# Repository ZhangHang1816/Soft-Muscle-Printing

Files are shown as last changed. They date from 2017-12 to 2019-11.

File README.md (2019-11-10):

# Soft-Muscle-Printing

This repository contains the code/data/model for printing Soft Artificial Muscle using Soft Muscle Printer.
The runnable jupyter notebook are [dog_bone muscle.ipynb](https://github.com/boxiXia/Soft-Muscle-Printing/blob/master/dog_bone%20muscle.ipynb) and [Soft_muscle_twisted spiral.ipynb](https://github.com/boxiXia/Soft-Muscle-Printing/blob/master/dog_bone%20muscle.ipynb)

### Graphical abstract
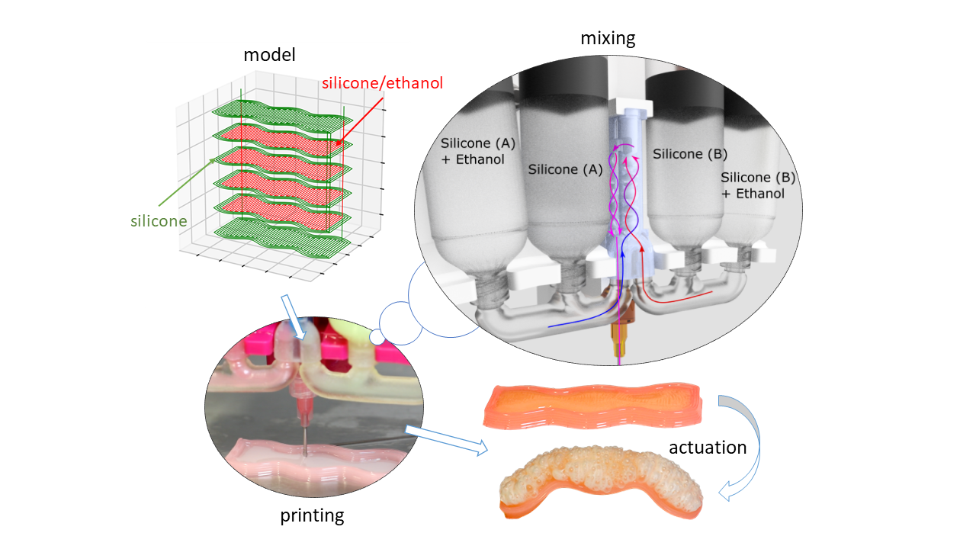
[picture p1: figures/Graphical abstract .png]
graphical abstract


### Photo of the soft muscle printer
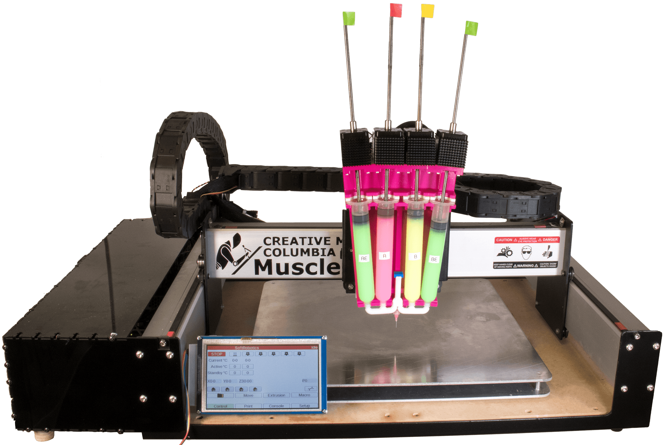
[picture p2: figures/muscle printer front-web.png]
Artificial muscle printer


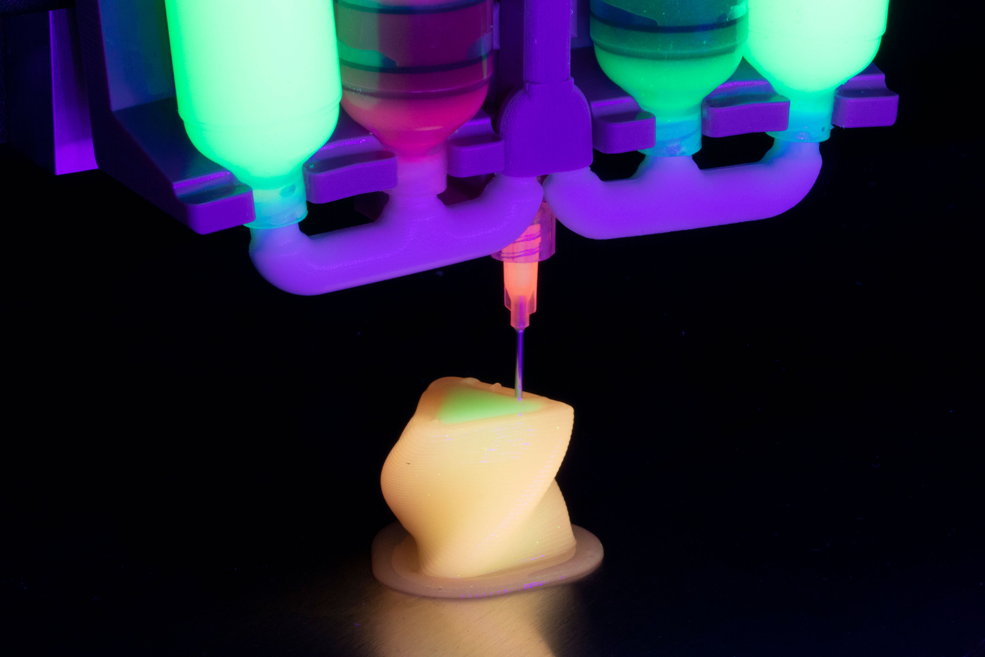
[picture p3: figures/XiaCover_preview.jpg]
printing rotating triangle


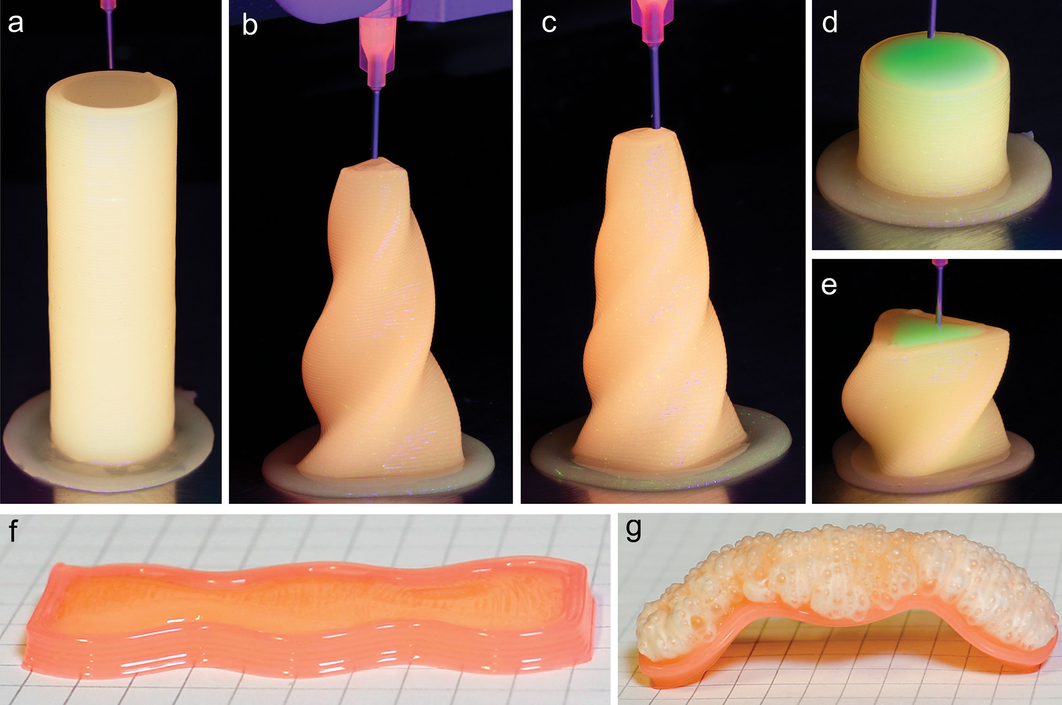
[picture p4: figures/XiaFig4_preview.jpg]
printed sturctures


### video of printing a muscle and actuating
supplementary - printing muscle and actuating (https://www.youtube.com/watch?v=KcunfdATq7U)

### video of printing complex structures
Supplementary - 3D Printing of Complex Shaped Structures (https://www.youtube.com/watch?v=6kZ5QKU3RHI)

### CAD and STL model of the mixer and electronics housing.
 
The raw Inventor model can be found in the [modeling](https://github.com/boxiXia/Soft-Muscle-Printing/tree/master/modeling) folder, which contains contains the 3d-printable and lasercut models to replicate the printer.

The mixer CAD model can be found in in [./modeling/mixer_design](https://github.com/boxiXia/Soft-Muscle-Printing/tree/master/modeling/mixer_design). The converted stl model can be found in [./modeling/mixer_design/stl_model](https://github.com/boxiXia/Soft-Muscle-Printing/tree/master/modeling/mixer_design/stl_model).
The CAD model for laser-cutting the electronics housing can be found in [modeling/lasercut_electronics_housing](https://github.com/boxiXia/Soft-Muscle-Printing/tree/master/modeling/lasercut_electronics_housing).
To open the CAD model (\*.ipt and \*.iam file), use [Autodesk Inventor 2019](https://www.autodesk.com/education/free-software/inventor-professional). The CAD models can also be found in [Grabcad](https://grabcad.com/library/soft-muscle-printer-1). 

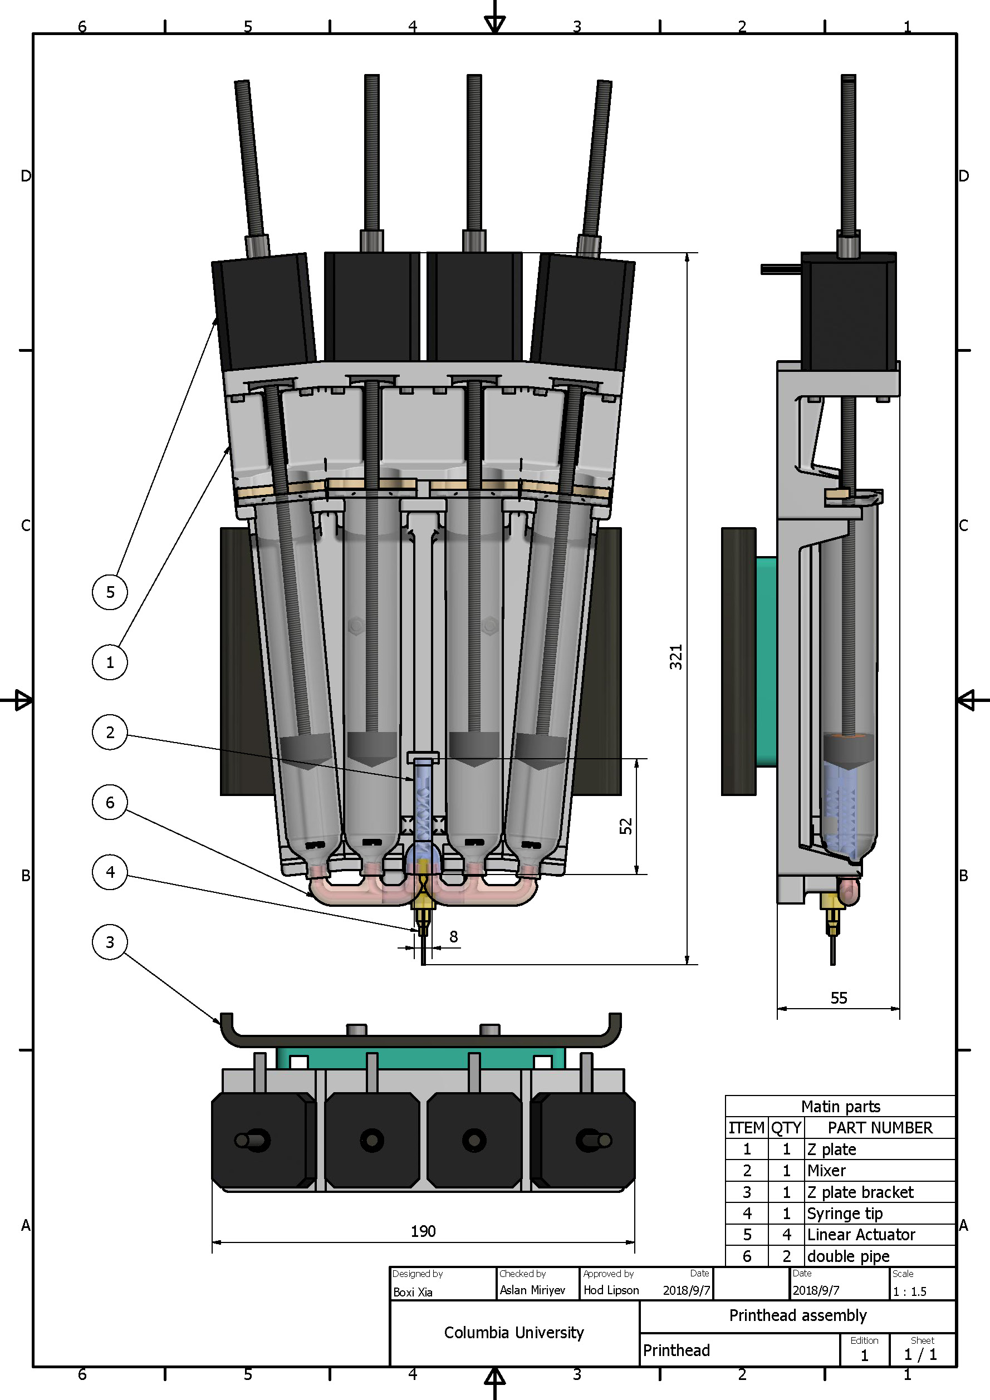
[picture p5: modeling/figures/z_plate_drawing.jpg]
assembly drwaing


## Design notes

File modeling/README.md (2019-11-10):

CAD model for the silicone muscle printer project @CreativeMachinesLab.

The folder "mixer_design" contains the Autodesk Inventor (2018) files for the mixing and printing module, the folder "stl_model" contains the exported ".stl" files of the printing module. The z plate assembly is printed with a Stratasys J750 printer in the Creative Machines Lab. The tubing is printed using "FLX9795-dm; Shore-A:95", the other parts are printed with "VeroPureWht." @boxiXia
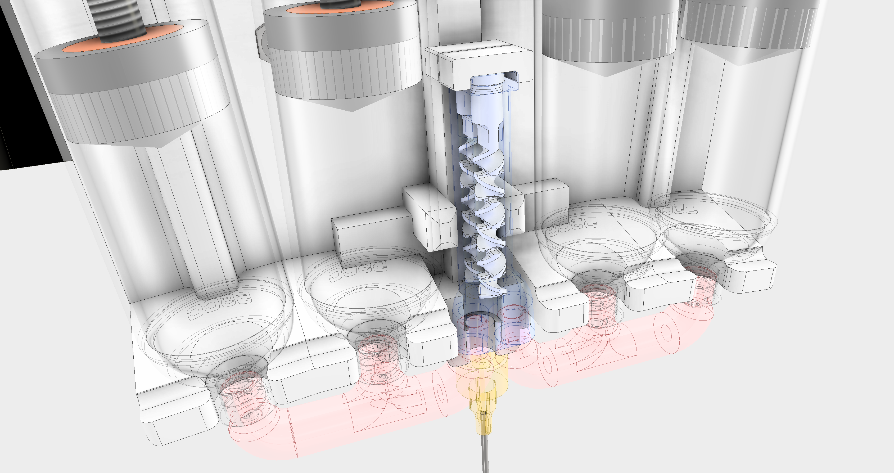
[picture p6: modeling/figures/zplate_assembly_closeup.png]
close up view of the z plate assembly


The folder "lasercut_electronics_housing" contains the electronic side mounting box model for the Shapeoko gantry. CAD files turned into two-dimensional drawing files are laser cut out of a 1/8 in a thick acrylic sheet. Two sheets about two feet long by 3 feet wide will be enough material for the entire assembly. The slots that connect the different sheets require 6-32 thread, ½ in long screws and 6-32 thread square nuts. Around 50 will be enough to assemble the housing. There are two square cutouts for installing fans used for cooling the control boards @jacobjoseph
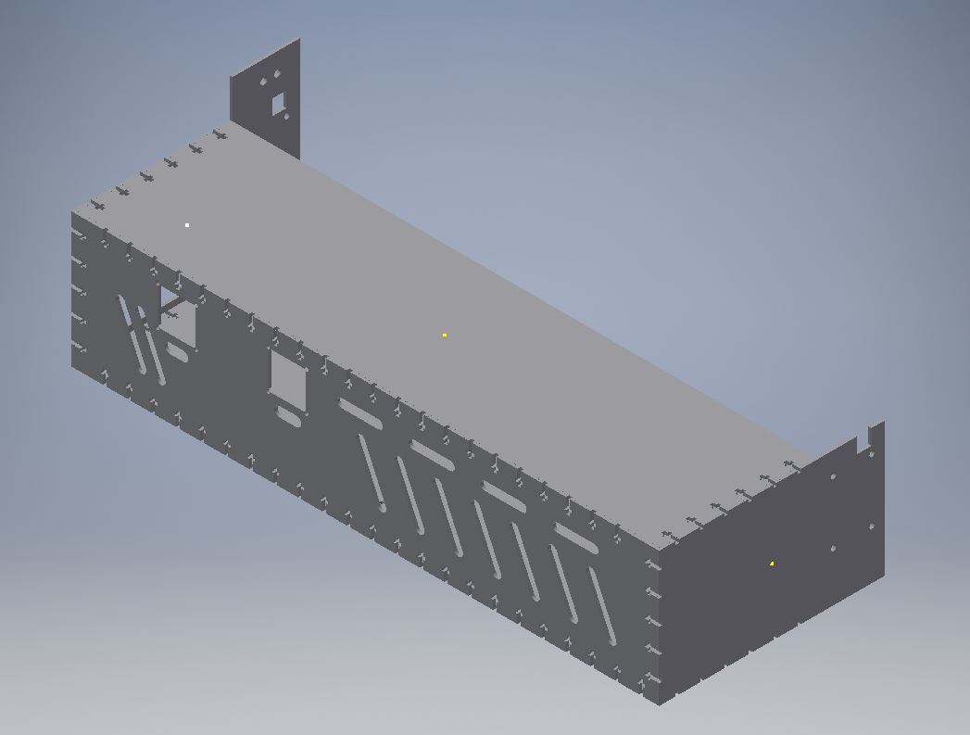
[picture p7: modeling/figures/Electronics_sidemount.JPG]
electronic side mount


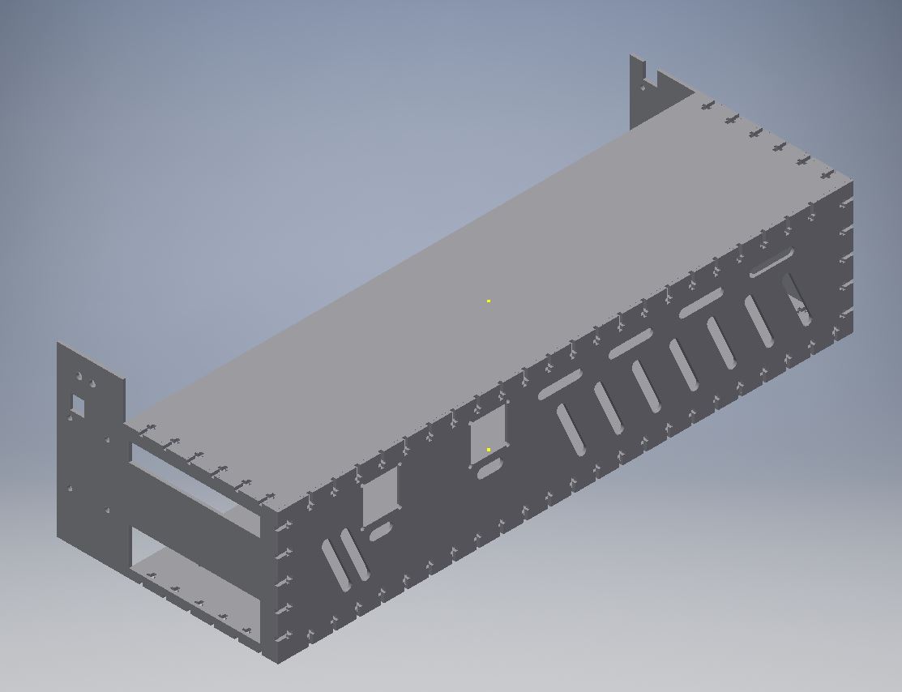
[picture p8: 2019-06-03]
modeling/figures/Electronics_sidemount_back.JPG

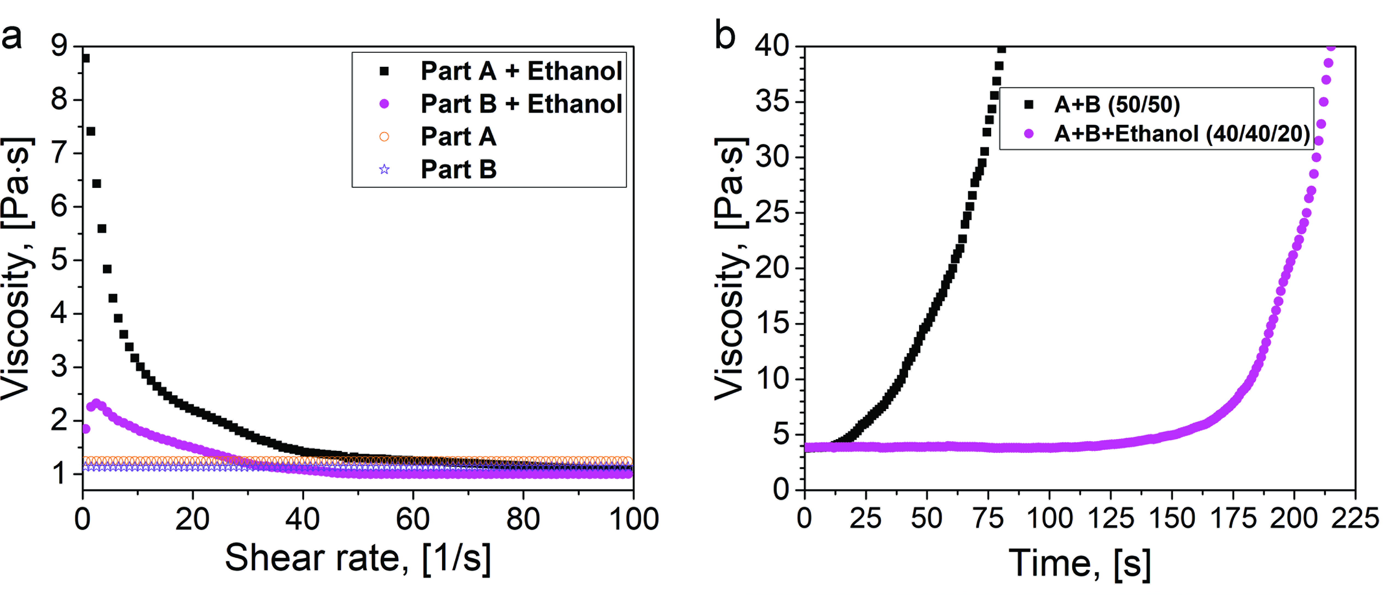
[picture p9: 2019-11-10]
figures/XiaFig5.tif

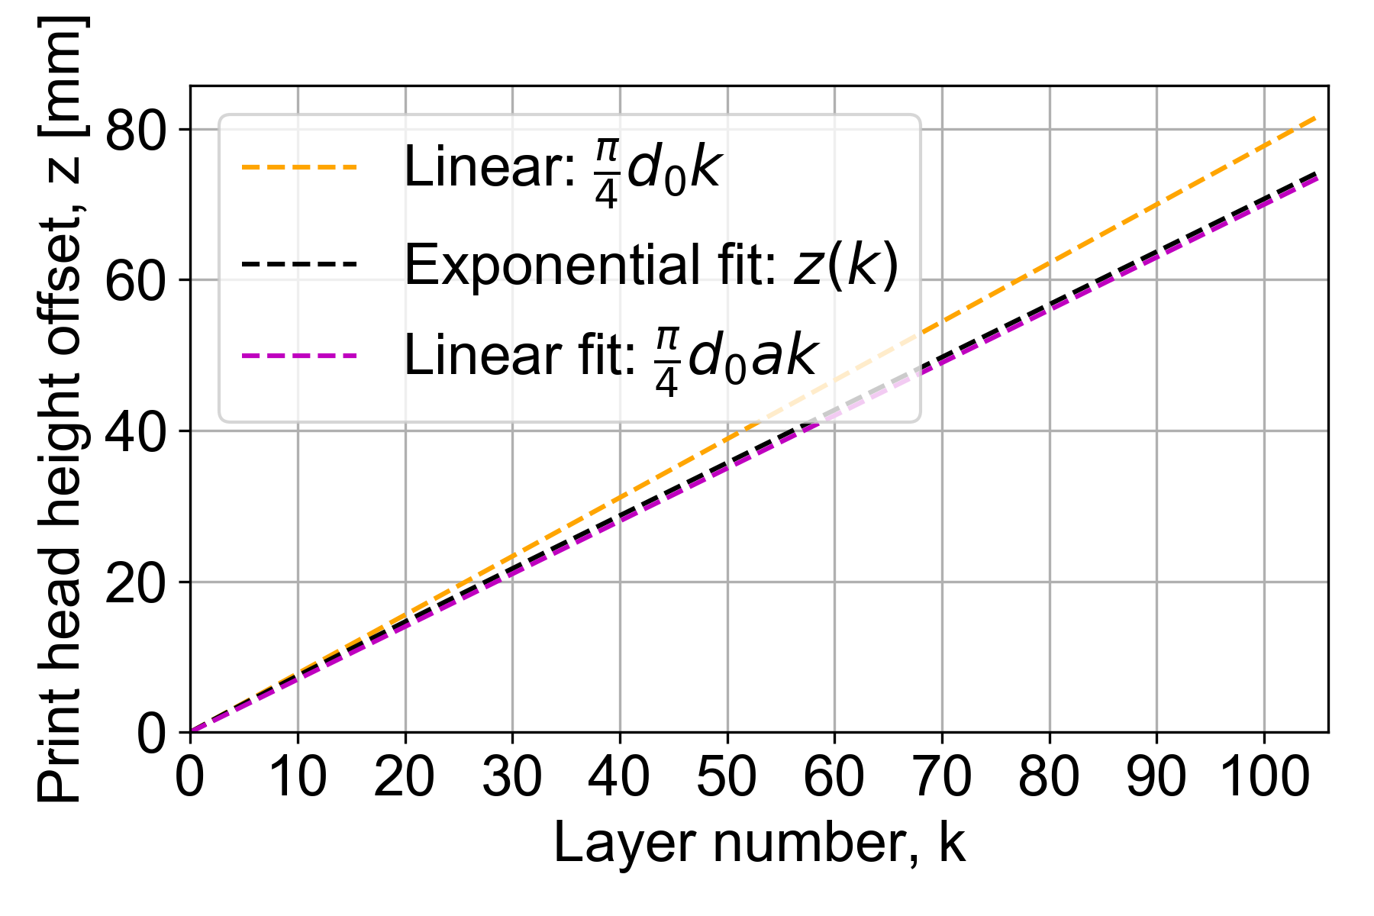
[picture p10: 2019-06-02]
figures/Z height Adjustment_a0.9_b0.1.png

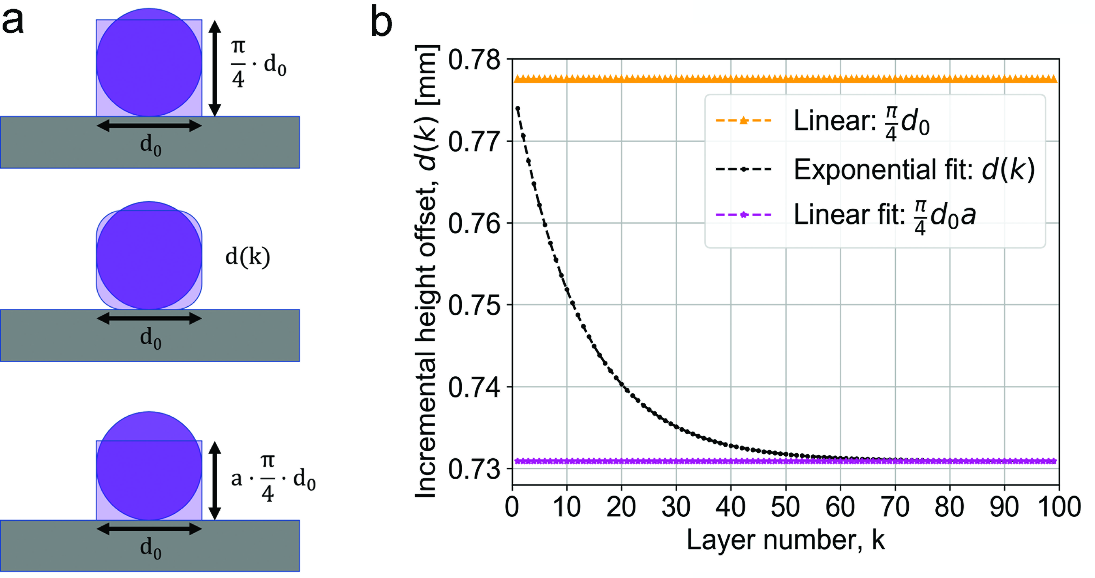
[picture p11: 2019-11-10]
figures/XiaFig3.tif

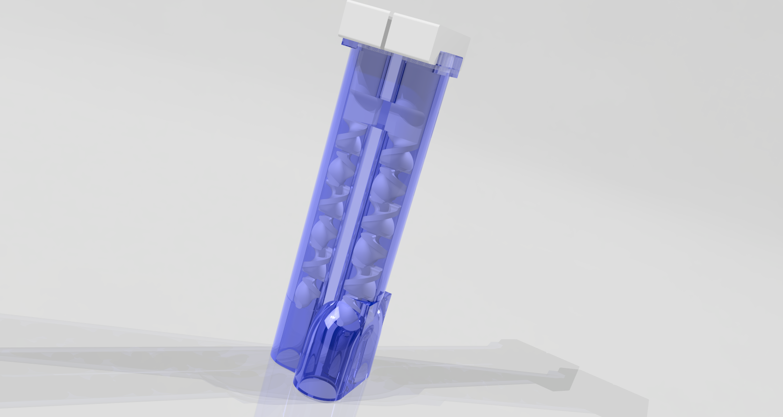
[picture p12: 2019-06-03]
modeling/figures/mixer.png

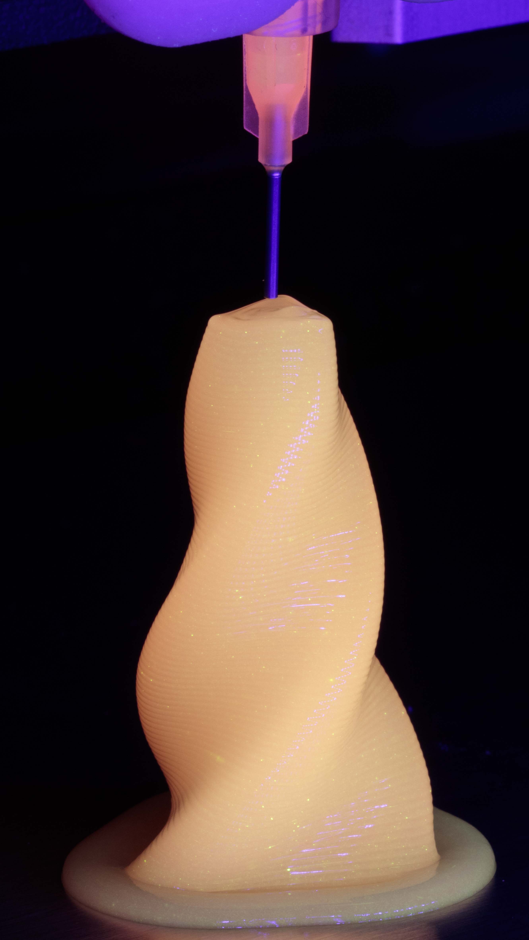
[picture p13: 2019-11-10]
figures/rotating triangle.jpg

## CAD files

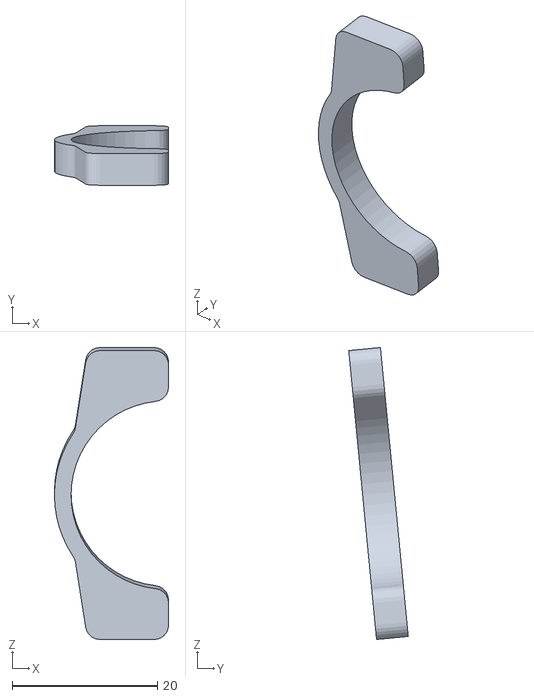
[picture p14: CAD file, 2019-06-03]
modeling/mixer_design/stl_model/zplate_assembly_syringe_stopper_x4.stl
15.7 x 8.21 x 40.2

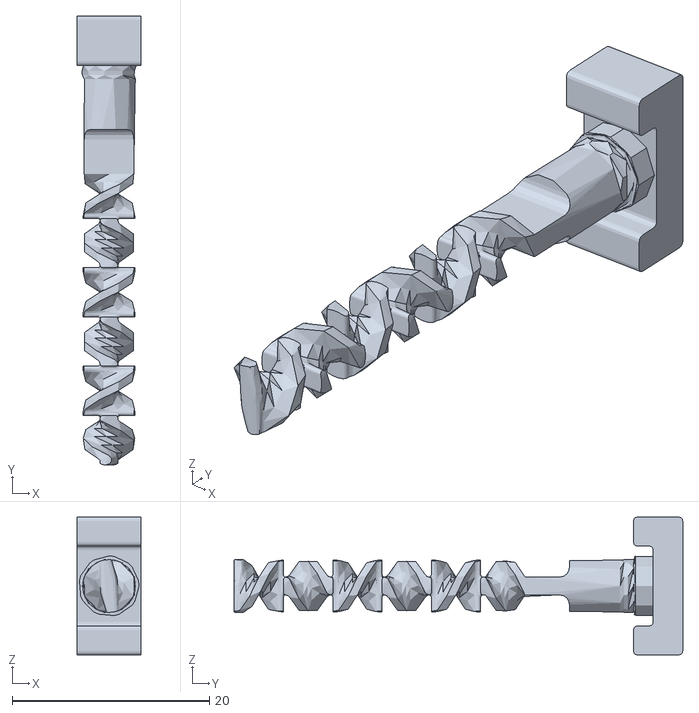
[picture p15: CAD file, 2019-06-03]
modeling/mixer_design/stl_model/zplate_assembly_mixer_core_x2.stl
6.50 x 45.5 x 14.0

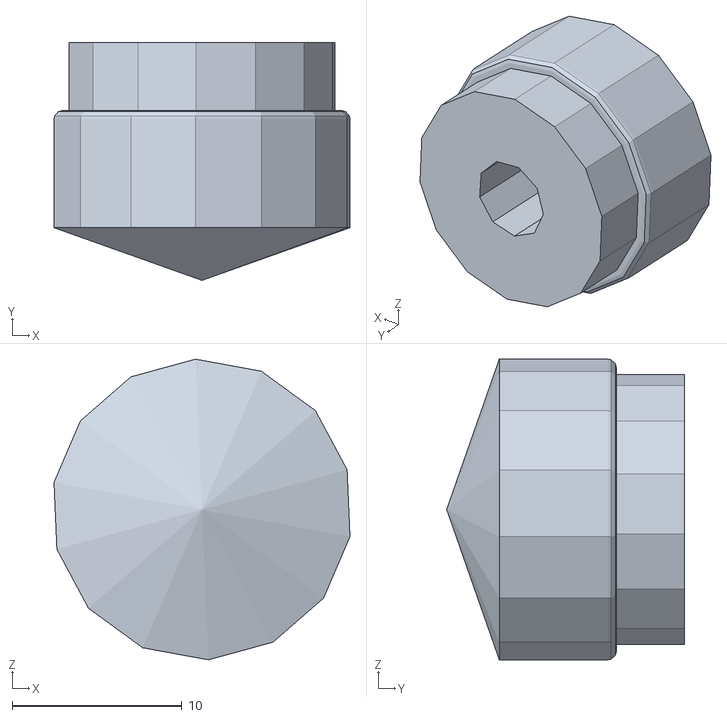
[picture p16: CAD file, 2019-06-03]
modeling/mixer_design/stl_model/zplate_assembly_plunger_adaptor_x4.stl
17.4 x 14.0 x 17.7

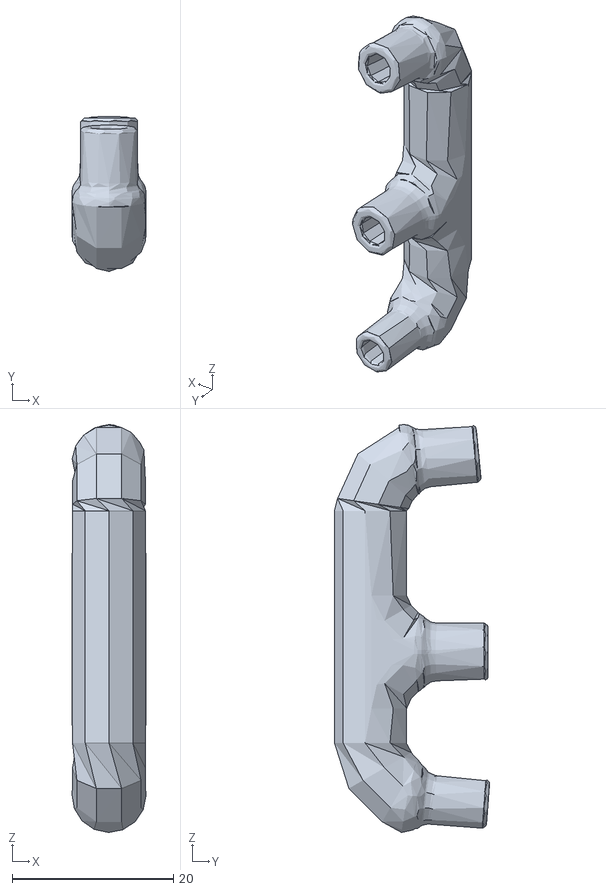
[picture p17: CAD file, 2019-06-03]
modeling/mixer_design/stl_model/zplate_assembly_doublePipe_v7.stl
9.20 x 19.3 x 50.7

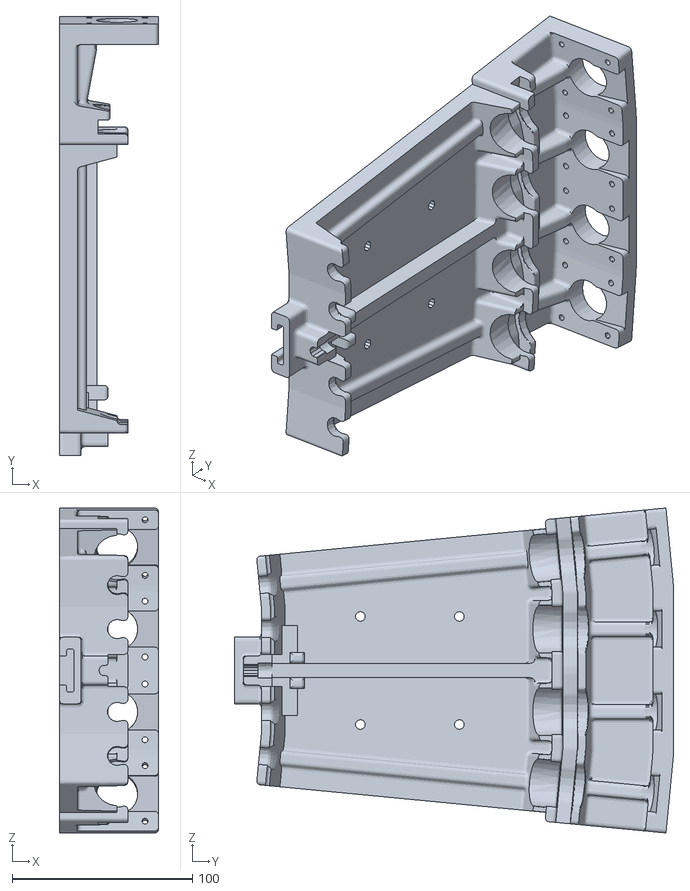
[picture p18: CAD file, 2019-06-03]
modeling/mixer_design/stl_model/zplate_assembly_30ml syringe holder.stl
55.0 x 244.0 x 180.5

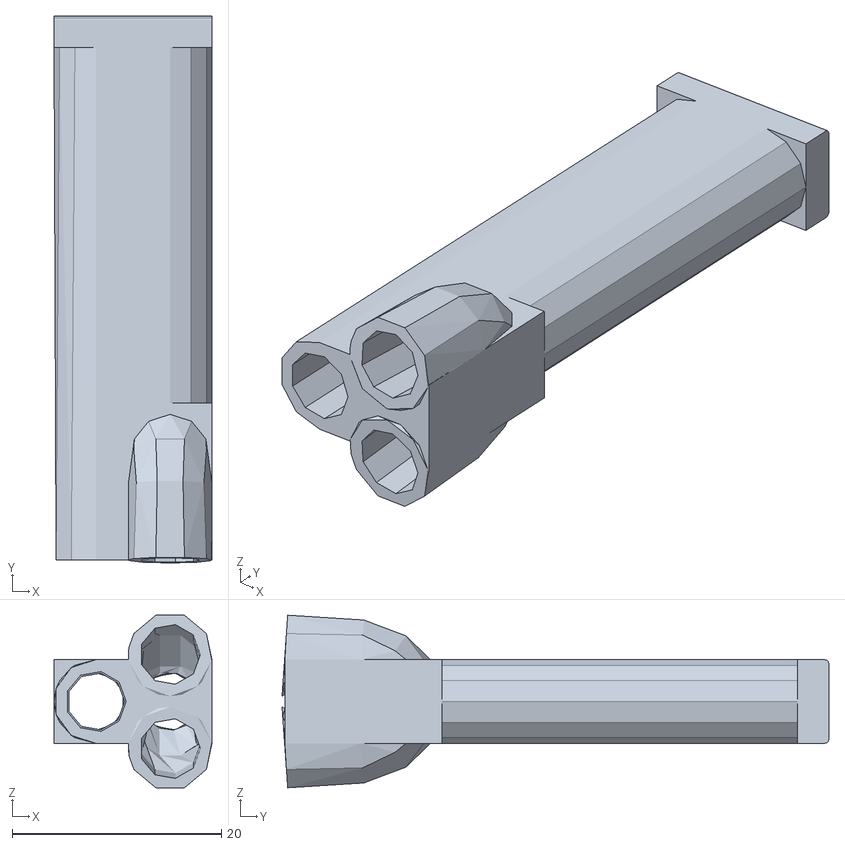
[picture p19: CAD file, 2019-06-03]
modeling/mixer_design/stl_model/zplate_assembly_mixer_cover.stl
15.1 x 52.3 x 16.5

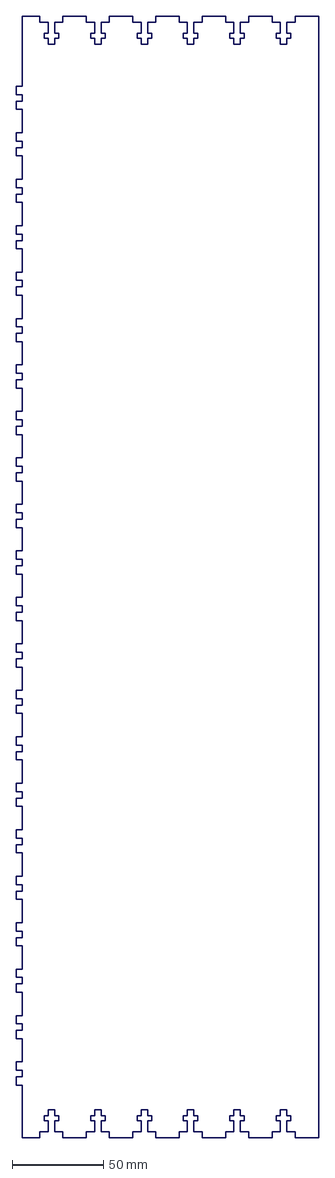
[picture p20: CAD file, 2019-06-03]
modeling/lasercut_electronics_housing/DXF/ElectronicsCase_top.DXF
165.1 x 612.8 mm

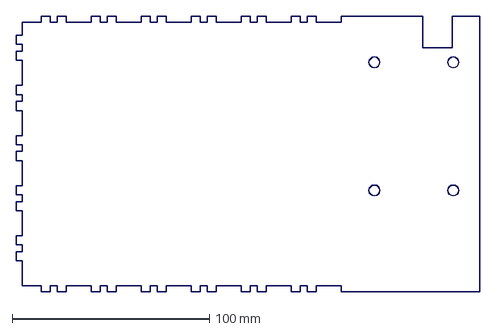
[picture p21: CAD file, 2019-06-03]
modeling/lasercut_electronics_housing/DXF/ElectronicsCase_front.DXF
235.3 x 140.0 mm

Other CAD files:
modeling/mixer_design/zplate_assembly.dwg
modeling/lasercut_electronics_housing/BoardMountingBracket.dwg
modeling/mixer_design/Templates/en-US/English/ANSI (in).dwg
modeling/mixer_design/Templates/en-US/Metric/DIN.dwg
modeling/mixer_design/Templates/en-US/Standard.dwg
modeling/mixer_design/Templates/English/am_ansi.dwg
modeling/mixer_design/Templates/Metric/BSI.dwg
modeling/mixer_design/Templates/standard.dwg
modeling/lasercut_electronics_housing/BoardMountingBracket_front.dwg
modeling/mixer_design/Templates/en-US/English/am_ansi.dwg
modeling/lasercut_electronics_housing/3DPrinterBracket_Top_Long_1%2F8.ipt
modeling/lasercut_electronics_housing/3DPrinterBracket_bottom_Long_1%2F8.ipt
modeling/lasercut_electronics_housing/3DPrinterBracket_end_long_1%2F8.ipt
modeling/lasercut_electronics_housing/3DprinterSideBracket_2.0_noLCD_1%2F8.ipt
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

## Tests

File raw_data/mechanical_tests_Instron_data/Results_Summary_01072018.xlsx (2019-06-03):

FORCE, N | Muscle With 20vol% Ethanol |  |  | STRAIN, % | Muscle With 20vol% Ethanol
 | Along | Across | CrissCross |  | Along | Across | CrissCross
1 | 10.62 | 16.58 | 12.64 | 1 | 276 | 317 | 304
2 | 11.7 | 10.273 | 12.68 | 2 | 274 | 258 | 305
3 | 11.79 | 11.03 | 16.8 | 3 | 275 | 277 | 335
4 | 11.83 | 12.17 | 20.33 | 4 | 280 | 311 | 389
5 | 9.59 | 7.07 | 17.928 | 5 | 250 | 249 | 385
AVERAGE | 11.11 | 11.42 | 16.08 | AVERAGE | 271 | 282.4 | 343.6
ST.DEV. | 0.98 | 3.45 | 3.37 | ST.DEV. | 11.96 | 30.64 | 41.55

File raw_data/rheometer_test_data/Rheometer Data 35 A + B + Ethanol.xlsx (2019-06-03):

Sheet: 35 A+B+Ethanol Test 1_1
Shear Rate 1/s | Shear Stress Pa | Instantaneous Viscosity Pas | Strain | Target Shear Rate 1/s | Percentage Deviation % | Temperature °C | Time s | Thrust g | Accumulated Time s | Notes
0.3084 | 0.8156 | 2.645 | 0.3123 | 0.3487 | 11.57 | 24.6 | 0.5056 | 0 | 0.5056
0.8137 | 2.633 | 3.236 | 1.143 | 0.8543 | 4.754 | 24.6 | 1.509 | 0 | 1.509
1.308 | 4.539 | 3.469 | 2.46 | 1.352 | 3.188 | 24.6 | 2.507 | 0 | 2.507
1.804 | 6.478 | 3.591 | 4.273 | 1.849 | 2.425 | 24.6 | 3.508 | 0 | 3.508
2.316 | 8.268 | 3.571 | 6.709 | 2.363 | 1.989 | 24.6 | 4.526 | 0 | 4.526
2.794 | 9.898 | 3.542 | 9.432 | 2.843 | 1.725 | 24.6 | 5.524 | 0 | 5.524
3.305 | 11.36 | 3.437 | 12.74 | 3.357 | 1.55 | 24.6 | 6.51 | 0 | 6.51
3.801 | 12.8 | 3.366 | 16.67 | 3.854 | 1.377 | 24.6 | 7.526 | 0 | 7.526
4.297 | 14.21 | 3.308 | 20.91 | 4.352 | 1.264 | 24.6 | 8.526 | 0 | 8.526
4.79 | 15.51 | 3.238 | 25.71 | 4.849 | 1.211 | 24.6 | 9.51 | 0 | 9.51
5.303 | 16.83 | 3.173 | 31.19 | 5.363 | 1.122 | 24.6 | 10.52 | 0 | 10.52
5.781 | 18.15 | 3.139 | 36.79 | 5.843 | 1.075 | 24.6 | 11.53 | 0 | 11.53
6.291 | 19.55 | 3.107 | 43.18 | 6.357 | 1.037 | 24.6 | 12.51 | 0 | 12.51
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

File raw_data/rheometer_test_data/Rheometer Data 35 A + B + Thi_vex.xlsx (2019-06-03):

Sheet: Ecoflex 35 A+B+ThiVex Test 1_1
Shear Rate 1/s | Shear Stress Pa | Instantaneous Viscosity Pas | Strain | Target Shear Rate 1/s | Percentage Deviation % | Temperature °C | Time s | Thrust g | Accumulated Time s | Notes
0.144 | 26.22 | 182 | 0.1712 | 0.2658 | 45.81 | 23.8 | 0.5049 | 0 | 0.5049
0.5862 | 97.28 | 166 | 0.7742 | 0.6029 | 2.77 | 23.8 | 1.508 | 0 | 1.508
0.8647 | 168.4 | 194.8 | 1.645 | 0.9344 | 7.461 | 23.8 | 2.508 | 0 | 2.508
1.192 | 286.2 | 240.1 | 2.853 | 1.266 | 5.827 | 23.8 | 3.507 | 0 | 3.507
1.598 | 431 | 269.8 | 4.498 | 1.597 | -0.01475 | 23.8 | 4.507 | 0 | 4.507
1.947 | 534.1 | 274.4 | 6.447 | 1.929 | -0.9162 | 23.8 | 5.507 | 0 | 5.507
2.276 | 574.7 | 252.5 | 8.728 | 2.26 | -0.7035 | 23.8 | 6.508 | 0 | 6.508
2.552 | 569.8 | 223.2 | 11.28 | 2.592 | 1.521 | 23.8 | 7.508 | 0 | 7.508
2.915 | 573.3 | 196.7 | 14.25 | 2.934 | 0.6718 | 23.8 | 8.508 | 0 | 8.508
3.182 | 568.6 | 178.7 | 17.44 | 3.266 | 2.58 | 23.8 | 9.508 | 0 | 9.508
3.613 | 576.5 | 159.5 | 21.04 | 3.597 | -0.4457 | 23.8 | 10.51 | 0 | 10.51
3.883 | 578.6 | 149 | 24.94 | 3.929 | 1.17 | 23.8 | 11.51 | 0 | 11.51
4.162 | 582 | 139.8 | 29.21 | 4.26 | 2.315 | 23.8 | 12.51 | 0 | 12.51
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

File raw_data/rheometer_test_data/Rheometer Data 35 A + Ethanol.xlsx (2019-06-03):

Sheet: 35 A + Ethanol Test 1
Shear Rate 1/s | Shear Stress Pa | Instantaneous Viscosity Pas | Strain | Target Shear Rate 1/s | Percentage Deviation % | Temperature °C | Time s | Thrust g | Accumulated Time s | Notes
0.5207 | 2.54 | 4.877 | 0.5301 | 0.5975 | 12.85 | 24.3 | 0.5044 | 0 | 0.5044
1.528 | 6.538 | 4.279 | 2.091 | 1.609 | 5.016 | 24.3 | 1.508 | 0 | 1.508
2.517 | 9.754 | 3.875 | 4.627 | 2.603 | 3.306 | 24.3 | 2.508 | 0 | 2.508
3.507 | 12.26 | 3.495 | 8.15 | 3.598 | 2.532 | 24.3 | 3.508 | 0 | 3.508
4.498 | 14.04 | 3.121 | 12.75 | 4.592 | 2.047 | 24.3 | 4.508 | 0 | 4.508
5.488 | 15.25 | 2.778 | 18.27 | 5.587 | 1.769 | 24.3 | 5.507 | 0 | 5.507
6.478 | 16.31 | 2.519 | 24.78 | 6.581 | 1.571 | 24.3 | 6.507 | 0 | 6.507
7.468 | 17.2 | 2.303 | 32.28 | 7.576 | 1.416 | 24.3 | 7.507 | 0 | 7.507
8.492 | 18.12 | 2.134 | 40.92 | 8.603 | 1.292 | 24.3 | 8.508 | 0 | 8.508
9.484 | 19.1 | 2.014 | 50.42 | 9.598 | 1.19 | 24.3 | 9.509 | 0 | 9.509
10.47 | 20.18 | 1.926 | 60.92 | 10.59 | 1.129 | 24.3 | 10.51 | 0 | 10.51
11.46 | 20.95 | 1.828 | 72.38 | 11.59 | 1.089 | 24.3 | 11.51 | 0 | 11.51
12.45 | 21.77 | 1.748 | 85.08 | 12.58 | 1.025 | 24.3 | 12.51 | 0 | 12.51
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

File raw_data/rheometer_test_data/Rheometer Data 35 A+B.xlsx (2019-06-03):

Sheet: 35 A + B Test 1_1
Shear Rate 1/s | Shear Stress Pa | Instantaneous Viscosity Pas | Strain | Target Shear Rate 1/s | Percentage Deviation % | Temperature °C | Time s | Thrust g | Accumulated Time s | Notes
0.5171 | 2.455 | 4.747 | 0.5288 | 0.5975 | 13.45 | 24.1 | 0.5047 | 0 | 0.5047
1.56 | 8.294 | 5.316 | 2.125 | 1.642 | 4.969 | 24.1 | 1.52 | 0 | 1.52
2.517 | 14.97 | 5.949 | 4.626 | 2.603 | 3.308 | 24.1 | 2.52 | 0 | 2.52
3.506 | 22.96 | 6.551 | 8.147 | 3.598 | 2.56 | 24.1 | 3.508 | 0 | 3.508
4.532 | 32.3 | 7.128 | 12.82 | 4.625 | 2.027 | 24.1 | 4.52 | 0 | 4.52
5.49 | 41.63 | 7.582 | 18.26 | 5.587 | 1.723 | 24.1 | 5.52 | 0 | 5.52
6.477 | 52.42 | 8.094 | 24.77 | 6.581 | 1.585 | 24.1 | 6.508 | 0 | 6.508
7.5 | 64.41 | 8.589 | 32.41 | 7.609 | 1.437 | 24.1 | 7.519 | 0 | 7.519
8.492 | 78.04 | 9.19 | 40.92 | 8.603 | 1.295 | 24.1 | 8.519 | 0 | 8.519
9.474 | 93.23 | 9.841 | 50.41 | 9.598 | 1.295 | 24.1 | 9.508 | 0 | 9.508
10.5 | 111.1 | 10.58 | 61.08 | 10.63 | 1.161 | 24.1 | 10.52 | 0 | 10.52
11.46 | 130 | 11.34 | 72.37 | 11.59 | 1.082 | 24.1 | 11.52 | 0 | 11.52
12.45 | 152.1 | 12.22 | 85.06 | 12.58 | 1.036 | 24.1 | 12.51 | 0 | 12.51
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

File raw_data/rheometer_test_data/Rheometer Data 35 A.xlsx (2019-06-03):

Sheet: 35 A Test 1
Shear Rate 1/s | Shear Stress Pa | Instantaneous Viscosity Pas | Strain | Target Shear Rate 1/s | Percentage Deviation % | Temperature °C | Time s | Thrust g | Accumulated Time s | Notes
0.5353 | 0.5838 | 1.09 | 0.5683 | 0.6141 | 12.82 | 24.2 | 0.5192 | 0 | 0.5192
1.527 | 1.806 | 1.182 | 2.094 | 1.609 | 5.053 | 24.2 | 1.523 | 0 | 1.523
2.517 | 3.089 | 1.227 | 4.629 | 2.603 | 3.292 | 24.2 | 2.511 | 0 | 2.511
3.541 | 4.33 | 1.223 | 8.289 | 3.631 | 2.48 | 24.2 | 3.526 | 0 | 3.526
4.53 | 5.512 | 1.217 | 12.75 | 4.625 | 2.055 | 24.2 | 4.525 | 0 | 4.525
5.521 | 6.71 | 1.215 | 18.27 | 5.62 | 1.76 | 24.2 | 5.511 | 0 | 5.511
6.511 | 7.947 | 1.221 | 25.02 | 6.614 | 1.569 | 24.2 | 6.524 | 0 | 6.524
7.468 | 9.068 | 1.214 | 32.28 | 7.576 | 1.428 | 24.2 | 7.524 | 0 | 7.524
8.49 | 10.27 | 1.21 | 40.93 | 8.603 | 1.318 | 24.2 | 8.509 | 0 | 8.509
9.514 | 11.44 | 1.203 | 50.76 | 9.631 | 1.212 | 24.2 | 9.524 | 0 | 9.524
10.47 | 12.45 | 1.189 | 60.9 | 10.59 | 1.129 | 24.2 | 10.52 | 0 | 10.52
11.46 | 13.65 | 1.191 | 72.39 | 11.59 | 1.092 | 24.2 | 11.51 | 0 | 11.51
12.48 | 14.56 | 1.166 | 85.49 | 12.61 | 1.036 | 24.2 | 12.52 | 0 | 12.52
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

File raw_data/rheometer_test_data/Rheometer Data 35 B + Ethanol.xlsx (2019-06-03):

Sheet: 35 B + Ethanol Test 1
Shear Rate 1/s | Shear Stress Pa | Instantaneous Viscosity Pas | Strain | Target Shear Rate 1/s | Percentage Deviation % | Temperature °C | Time s | Thrust g | Accumulated Time s | Notes
0.518 | 1.006 | 1.942 | 0.5315 | 0.5975 | 13.3 | 23.9 | 0.5044 | 0 | 0.5044
1.528 | 3.49 | 2.284 | 2.093 | 1.609 | 5.031 | 23.9 | 1.507 | 0 | 1.507
2.519 | 6.071 | 2.411 | 4.628 | 2.603 | 3.245 | 23.9 | 2.507 | 0 | 2.507
3.508 | 8.301 | 2.367 | 8.153 | 3.598 | 2.497 | 23.9 | 3.507 | 0 | 3.507
4.497 | 10.11 | 2.249 | 12.75 | 4.592 | 2.076 | 23.9 | 4.508 | 0 | 4.508
5.493 | 11.53 | 2.1 | 18.27 | 5.587 | 1.683 | 23.9 | 5.508 | 0 | 5.508
6.48 | 12.87 | 1.987 | 24.78 | 6.581 | 1.538 | 23.9 | 6.507 | 0 | 6.507
7.468 | 14.64 | 1.96 | 32.29 | 7.576 | 1.424 | 23.9 | 7.507 | 0 | 7.507
8.491 | 16.19 | 1.907 | 40.93 | 8.603 | 1.31 | 23.9 | 8.507 | 0 | 8.507
9.48 | 17.62 | 1.859 | 50.43 | 9.598 | 1.227 | 23.9 | 9.507 | 0 | 9.507
10.47 | 18.9 | 1.805 | 60.9 | 10.59 | 1.136 | 23.9 | 10.51 | 0 | 10.51
11.46 | 20.34 | 1.775 | 72.39 | 11.59 | 1.084 | 23.9 | 11.51 | 0 | 11.51
12.45 | 21.49 | 1.726 | 85.07 | 12.58 | 1.036 | 23.9 | 12.51 | 0 | 12.51
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

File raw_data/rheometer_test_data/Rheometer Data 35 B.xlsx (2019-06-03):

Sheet: 35 B Test 1
Shear Rate 1/s | Shear Stress Pa | Instantaneous Viscosity Pas | Strain | Target Shear Rate 1/s | Percentage Deviation % | Temperature °C | Time s | Thrust g | Accumulated Time s | Notes
0.536 | 0.5736 | 1.07 | 0.533 | 0.6141 | 12.71 | 24.3 | 0.5074 | 0 | 0.5074
1.56 | 1.809 | 1.159 | 2.162 | 1.642 | 4.953 | 24.3 | 1.527 | 0 | 1.527
2.518 | 2.946 | 1.17 | 4.628 | 2.603 | 3.282 | 24.3 | 2.526 | 0 | 2.526
3.508 | 4.117 | 1.174 | 8.151 | 3.598 | 2.502 | 24.3 | 3.512 | 0 | 3.512
4.531 | 5.29 | 1.168 | 12.92 | 4.625 | 2.042 | 24.3 | 4.526 | 0 | 4.526
5.52 | 6.496 | 1.177 | 18.27 | 5.62 | 1.77 | 24.3 | 5.526 | 0 | 5.526
6.511 | 7.622 | 1.171 | 24.79 | 6.614 | 1.559 | 24.3 | 6.512 | 0 | 6.512
7.502 | 8.827 | 1.177 | 32.55 | 7.609 | 1.397 | 24.3 | 7.526 | 0 | 7.526
8.492 | 10 | 1.178 | 40.92 | 8.603 | 1.291 | 24.3 | 8.526 | 0 | 8.526
9.483 | 11.15 | 1.175 | 50.42 | 9.598 | 1.199 | 24.3 | 9.512 | 0 | 9.512
10.51 | 12.38 | 1.179 | 61.28 | 10.63 | 1.135 | 24.3 | 10.53 | 0 | 10.53
11.46 | 13.47 | 1.176 | 72.39 | 11.59 | 1.086 | 24.3 | 11.53 | 0 | 11.53
12.48 | 14.8 | 1.185 | 85.07 | 12.61 | 1.042 | 24.3 | 12.51 | 0 | 12.51
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

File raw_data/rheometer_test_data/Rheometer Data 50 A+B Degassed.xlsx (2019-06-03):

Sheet: Ecoflex-0050 A+B Degassed #1
Shear Rate 1/s | Shear Stress Pa | Instantaneous Viscosity Pas | Strain | Target Shear Rate 1/s | Percentage Deviation % | Temperature °C | Time s | Thrust g | Accumulated Time s | Notes
0.4094 | 23.64 | 57.75 | 0.4468 | 0.5975 | 31.48 | 24.7 | 0.5047 | 0 | 0.5047
1.617 | 96.7 | 59.8 | 2.101 | 1.609 | -0.5347 | 24.7 | 1.508 | 0 | 1.508
2.538 | 102.1 | 40.24 | 4.73 | 2.636 | 3.723 | 24.7 | 2.522 | 0 | 2.522
3.515 | 101.5 | 28.88 | 8.16 | 3.598 | 2.301 | 24.7 | 3.522 | 0 | 3.522
4.493 | 97.29 | 21.66 | 12.76 | 4.592 | 2.168 | 24.7 | 4.507 | 0 | 4.507
5.532 | 95.29 | 17.23 | 18.47 | 5.62 | 1.56 | 24.7 | 5.521 | 0 | 5.521
6.487 | 94.9 | 14.63 | 24.78 | 6.581 | 1.428 | 24.7 | 6.522 | 0 | 6.522
7.484 | 86.89 | 11.61 | 32.31 | 7.576 | 1.211 | 24.7 | 7.508 | 0 | 7.508
8.511 | 72.69 | 8.541 | 41.23 | 8.637 | 1.454 | 24.7 | 8.522 | 0 | 8.522
9.468 | 70.78 | 7.476 | 50.42 | 9.598 | 1.357 | 24.7 | 9.521 | 0 | 9.521
10.46 | 72.23 | 6.903 | 60.91 | 10.59 | 1.217 | 24.7 | 10.51 | 0 | 10.51
11.5 | 76.05 | 6.613 | 72.79 | 11.62 | 1.029 | 24.7 | 11.52 | 0 | 11.52
12.45 | 79.56 | 6.39 | 85.07 | 12.58 | 1.043 | 24.7 | 12.52 | 0 | 12.52
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

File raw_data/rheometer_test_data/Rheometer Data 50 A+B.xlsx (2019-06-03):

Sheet: Ecoflec-0050 A+B(0s delay)#1
Shear Rate 1/s | Shear Stress Pa | Instantaneous Viscosity Pas | Strain | Target Shear Rate 1/s | Percentage Deviation % | Temperature °C | Time s | Thrust g | Accumulated Time s | Notes
0.5174 | 2.259 | 4.366 | 0.53 | 0.5975 | 13.41 | 24.5 | 0.5047 | 0 | 0.5047
1.527 | 6.886 | 4.511 | 2.093 | 1.609 | 5.09 | 24.5 | 1.508 | 0 | 1.508
2.515 | 11.57 | 4.6 | 4.628 | 2.603 | 3.369 | 24.5 | 2.507 | 0 | 2.507
3.505 | 16.22 | 4.628 | 8.149 | 3.598 | 2.573 | 24.5 | 3.508 | 0 | 3.508
4.499 | 20.92 | 4.65 | 12.74 | 4.592 | 2.038 | 24.5 | 4.508 | 0 | 4.508
5.489 | 25.67 | 4.677 | 18.27 | 5.587 | 1.741 | 24.5 | 5.508 | 0 | 5.508
6.477 | 30.44 | 4.7 | 24.78 | 6.581 | 1.585 | 24.5 | 6.507 | 0 | 6.507
7.47 | 35.08 | 4.697 | 32.28 | 7.576 | 1.402 | 24.5 | 7.507 | 0 | 7.507
8.493 | 40.27 | 4.741 | 40.93 | 8.603 | 1.278 | 24.5 | 8.508 | 0 | 8.508
9.48 | 44.99 | 4.746 | 50.42 | 9.598 | 1.232 | 24.5 | 9.508 | 0 | 9.508
10.47 | 49.78 | 4.755 | 60.91 | 10.59 | 1.147 | 24.5 | 10.51 | 0 | 10.51
11.46 | 54.67 | 4.769 | 72.38 | 11.59 | 1.065 | 24.5 | 11.51 | 0 | 11.51
12.45 | 59.76 | 4.799 | 85.08 | 12.58 | 1.027 | 24.5 | 12.51 | 0 | 12.51
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

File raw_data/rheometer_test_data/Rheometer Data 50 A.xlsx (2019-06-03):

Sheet: Ecoflex_0050 A #1
Time s | Temperature °C | Target Shear Rate 1/s | Shear Rate 1/s | Percentage Deviation % | Shear Stress Pa | Viscosity Pas | Thrust g | Accumulated Time s | Real Time s | Angular Velocity rad/s | Torque Nm | Displacement rad | Notes
10.05 | 23.6 | 0.7314 | 0.7281 | 0.45 | 1.618 | 2.223 | 0 | 10.05 | 10.05 | 0.008737 | 4.966e-06 | 0
25.16 | 23.6 | 0.7314 | 0.7281 | 0.45 | 1.683 | 2.312 | 0 | 25.16 | 25.16 | 0.008737 | 5.165e-06 | 0
40.26 | 23.6 | 0.7314 | 0.7282 | 0.44 | 1.687 | 2.317 | 0 | 40.26 | 40.26 | 0.008738 | 5.176e-06 | 0
55.35 | 23.6 | 0.7314 | 0.7281 | 0.44 | 1.688 | 2.318 | 0 | 55.35 | 55.35 | 0.008738 | 5.18e-06 | 0
70.46 | 23.6 | 0.7314 | 0.7281 | 0.45 | 1.739 | 2.388 | 0 | 70.46 | 70.46 | 0.008737 | 5.335e-06 | 0
85.56 | 23.6 | 0.7314 | 0.7281 | 0.44 | 1.713 | 2.353 | 0 | 85.56 | 85.56 | 0.008738 | 5.256e-06 | 0
100.6 | 23.6 | 0.7314 | 0.7281 | 0.45 | 1.761 | 2.418 | 0 | 100.6 | 100.6 | 0.008737 | 5.402e-06 | 0
115.8 | 23.6 | 0.7314 | 0.7281 | 0.44 | 1.795 | 2.465 | 0 | 115.8 | 115.8 | 0.008737 | 5.508e-06 | 0
130.9 | 23.6 | 0.7314 | 0.7281 | 0.45 | 1.794 | 2.463 | 0 | 130.9 | 130.9 | 0.008737 | 5.504e-06 | 0
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

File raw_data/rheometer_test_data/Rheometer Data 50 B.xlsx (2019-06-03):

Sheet: Ecoflex-0050 B #1
Shear Rate 1/s | Shear Stress Pa | Viscosity Pas | Target Shear Rate 1/s | Percentage Deviation % | Temperature °C | Time s | Thrust g | Accumulated Time s | Angular Velocity rad/s
0.7282 | 0.7425 | 1.02 | 0.7314 | 0.4369 | 23.9 | 10.02 | 0 | 10.02 | 0.008738
0.7281 | 0.7562 | 1.039 | 0.7314 | 0.445 | 24 | 25.12 | 0 | 25.12 | 0.008737
0.7281 | 0.7689 | 1.056 | 0.7314 | 0.4497 | 24 | 40.21 | 0 | 40.21 | 0.008737
0.7281 | 0.7735 | 1.062 | 0.7314 | 0.4487 | 24 | 55.3 | 0 | 55.3 | 0.008737
0.7282 | 0.8175 | 1.123 | 0.7314 | 0.4414 | 24 | 70.41 | 0 | 70.41 | 0.008738
0.7281 | 0.8194 | 1.125 | 0.7314 | 0.4505 | 24 | 85.51 | 0 | 85.51 | 0.008737
0.7281 | 0.8959 | 1.23 | 0.7314 | 0.4423 | 24 | 100.6 | 0 | 100.6 | 0.008738
0.7281 | 0.9406 | 1.292 | 0.7314 | 0.4478 | 24 | 115.7 | 0 | 115.7 | 0.008737
0.7281 | 0.982 | 1.349 | 0.7314 | 0.4478 | 24 | 130.8 | 0 | 130.8 | 0.008737
0.7281 | 1.033 | 1.419 | 0.7314 | 0.4466 | 24 | 145.9 | 0 | 145.9 | 0.008737
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

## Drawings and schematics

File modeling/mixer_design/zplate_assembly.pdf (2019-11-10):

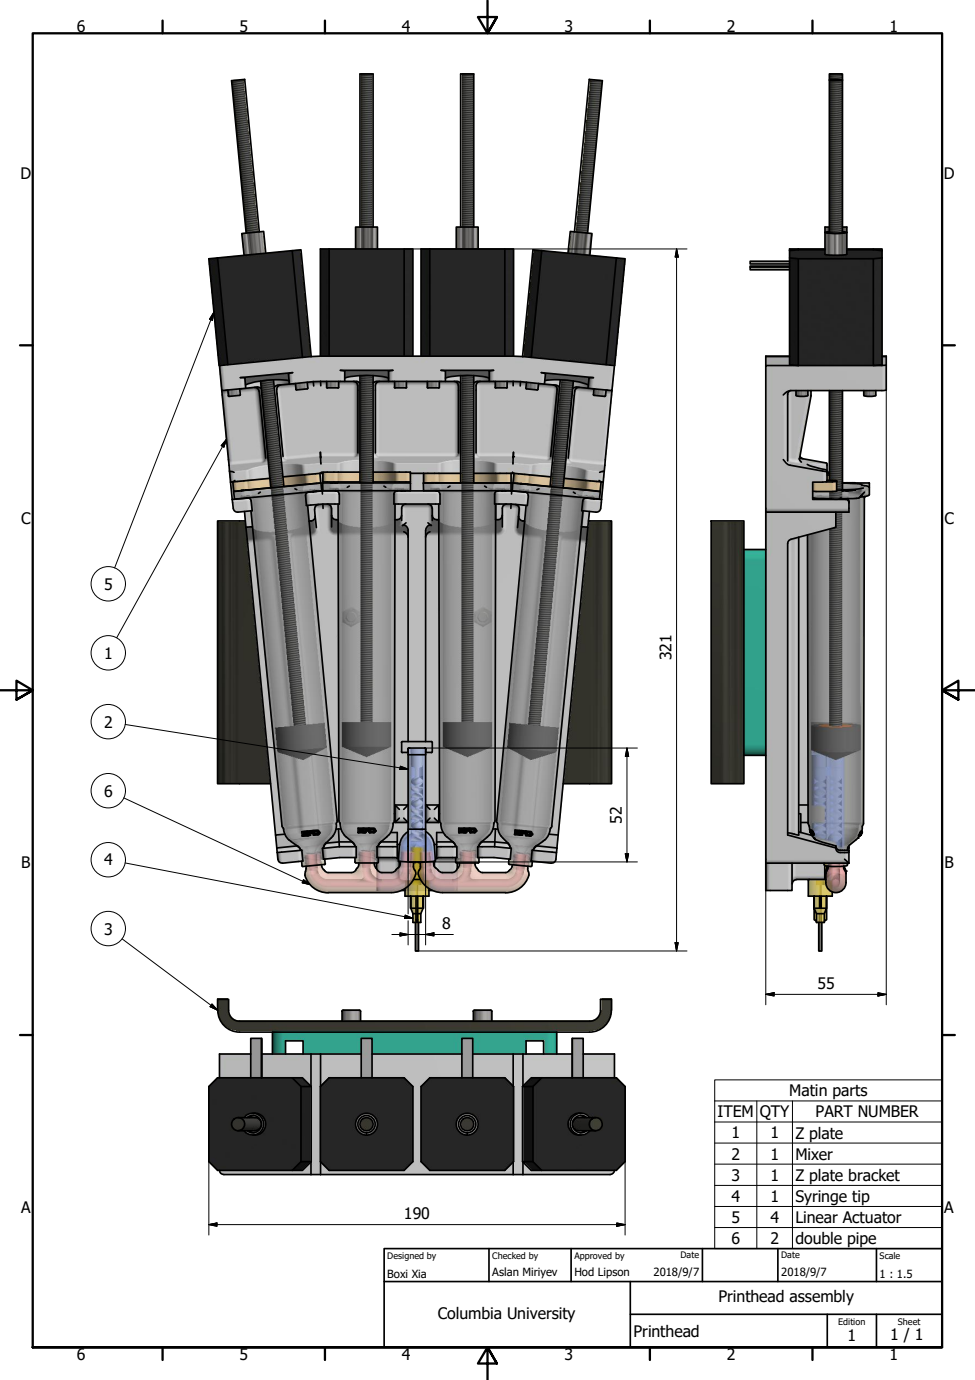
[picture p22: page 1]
Matin parts

ITEM | QTY | PART NUMBER
1 | 1 | Z plate
2 | 1 | Mixer
3 | 1 | Z plate bracket
4 | 1 | Syringe tip
5 | 4 | Linear Actuator
6 | 2 | double pipe

Designed by Boxi Xia | Checked by Aslan Miriyev | Approved by Date Hod Lipson 2018/9/7 | Date 2018/9/7 | Scale 1 : 1.5

Columbia University | Printhead assembly

Printhead | Edition 1 | Sheet 1 / 1

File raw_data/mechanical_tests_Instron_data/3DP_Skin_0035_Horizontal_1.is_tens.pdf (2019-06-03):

## Specimen 1 to 1

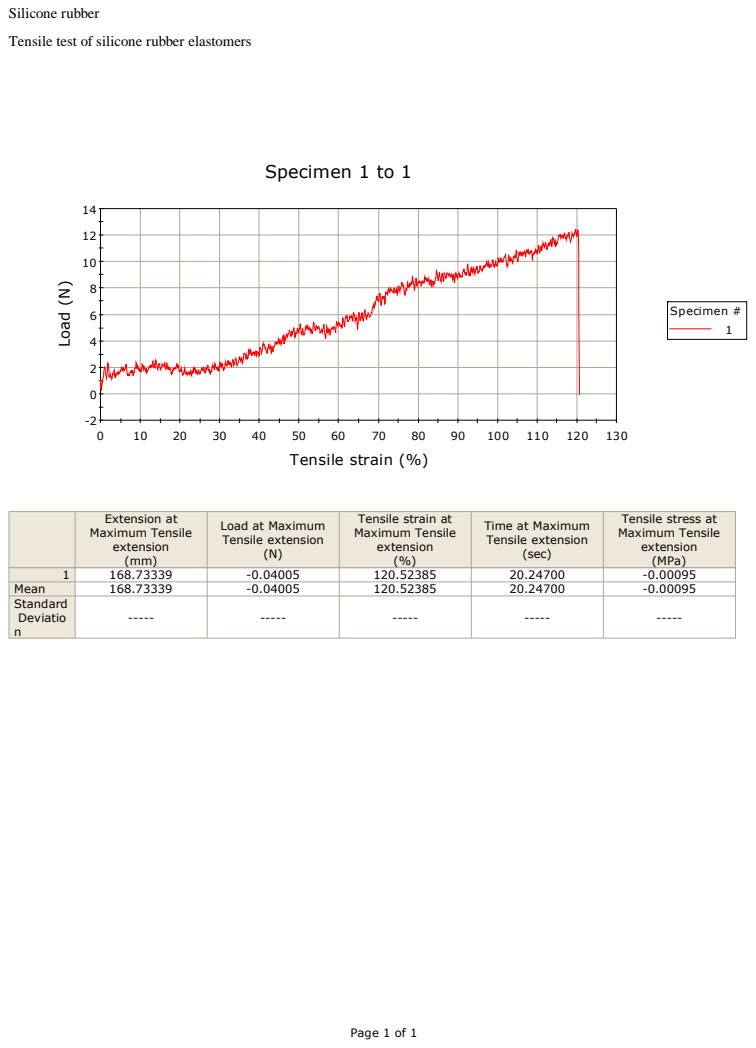
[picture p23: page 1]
Silicone rubber; Load (N); Tensile strain (%); Specimen #

Tensile test of silicone rubber elastomers

Extension at Maximum Tensile extension (mm) | Load at Maximum Tensile extension (N) | Tensile strain at Maximum Tensile extension (%) | Time at Maximum Tensile extension (sec) | Tensile stress at Maximum Tensile extension (MPa)

Mean | 168.73339 | -0.04005 | 120.52385 | 20.24700 | -0.00095
Standard Deviatio n | ----- | ----- | ----- | ----- | -----

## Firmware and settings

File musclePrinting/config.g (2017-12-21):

; Configuration file for Duet WiFi (firmware version 1.17)
; executed by the firmware on start-up
;
; generated by RepRapFirmware Configuration Tool on Mon Oct 16 2017 21:54:36 GMT-0400 (Eastern Daylight Time)

; General preferences
M111 S0 ; Debugging off
G21 ; Work in millimetres
G90 ; Send absolute coordinates...
M83 ; ...but relative extruder moves
M555 P1 ; Set firmware compatibility to look like RepRapFirmare
M208 X-200 Y-200 Z0 S1 ; Set axis minima
M208 X200 Y200 Z80 S0 ; Set axis maxima

; Endstops
M574 X2 Y2 Z2 S0 ; Define active low and unused microswitches
M558 P0 X0 Y0 Z0 H5 F120 T6000 ; Set Z probe type to switch, the axes for which it is used and the probe + travel speeds
G31 P600 X0 Y0 Z2.5 ; Set Z probe trigger value, offset and trigger height
M557 X15:385 Y15:385 S20 ; Define mesh grid

; Drives
M569 P0 S0 ; Drive 0 goes backwards
M569 P1 S1 ; Drive 1 goes forwards
M569 P2 S0 ; Drive 2 goes backwards
M569 P3 S0 ; Drive 3 goes backwards
M569 P4 S0 ; Drive 4 goes backwards
M569 P5 S0 ; Drive 5 goes backwards
M569 P6 S0 ; Drive 6 goes backwards
M584 X0 Y2 Z1 E3:4:5:6 ; Apply custom drive mapping
M350 X128 Y128 Z128 E128:128:128:128 I0 ; Configure microstepping without interpolation
M92 X1280 Y1280 Z1280 E25600:25600:25600:25600 ; Set steps per mm
M566 X900 Y900 Z900 E1200:1200:1200:1200 ; Set maximum instantaneous speed changes (mm/min)
M203 X6000 Y6000 Z240 E1500:1500:1500:1500 ; Set maximum speeds (mm/min)
M201 X500 Y500 Z500 E250:250:250:250 ; Set accelerations (mm/s^2)
M906 X2000 Y2000 Z2000 E1800:1800:1800:1800 I80 ; Set motor currents (mA) and motor idle factor in per cent
M84 S500 ; Set idle timeout

;Temperature
M305 P0 X201 ; heater 0 (which is normally the Bed heater) it should sense the temperature using the RTD2 of the PT100 board
M141 H1 ; heater 1 is the chamber heater
M305 P1 X200 ; heater 1 (which is the first hot end heater) should sense the temperature using the RTD1 of the PT100 Board 

; Heaters
M143 H1 S80 ; Set maximum heater 1 temperature to 80C
;M301 H1 P-1 ; use bang-bang control for heater 1 

M301 H1 P166.8, I0.650, D388.5 T3.3 S0.2;
; USE: "M303 H1 P0.2 S70" to auto-tune refer:
;M301 H1 P685.9 I11.778 D238.3 T1 S0.36 ; PID control for heater one, P = proportional gain, D = derivative gain, I = integral gain, T = additional PWM, S = PWM scaling factor
M141 S40 ; turn on chamber heater to 40C
M141 H1 ; return control to the host immediately
M140 H-1 ; Disable heated bed

; Tools
M563 P0 D0; Define tool 0
G10 P0 X0 Y0 Z0 ; Set tool 0 axis offsets
;G10 P0 R0 S0 ; Set initial tool 0 active and standby temperatures to 0C
M563 P1 D1; Define tool 1
G10 P1 X0 Y0 Z0 ; Set tool 1 axis offsets
;G10 P1 R0 S0 ; Set initial tool 1 active and standby temperatures to 0C
M563 P2 D2; Define tool 2
G10 P2 X0 Y0 Z0 ; Set tool 2 axis offsets
;G10 P2 R0 S0 ; Set initial tool 2 active and standby temperatures to 0C
M563 P3 D3; Define tool 3
G10 P3 X0 Y0 Z0 ; Set tool 3 axis offsets
;G10 P3 R0 S0 ; Set initial tool 3 active and standby temperatures to 0C
M563 P4 D0:1:2:3; Define tool 4
G10 P4 X0 Y0 Z0 ; Set tool 4 axis offsets
;G10 P4 R0 S0 ; Set initial tool 4 active and standby temperatures to 0C
;M568 P4 S1 ; Enable mixing for tool 4
;M567 P4 E0.25:0.25:0.25:0.25 ; Set mixing ratios for tool 4

; Network
M550 PSoftRobotics ; Set machine name
M552 S1 ; Enable network
; Access point is configured manually via M587 by the user
M586 P0 S1 ; Enable HTTP
M586 P1 S0 ; Disable FTP
M586 P2 S0 ; Disable Telnet

; Fans
M106 P0 S1 I0 F500 H T32 ; Set fan 0 value, PWM signal inversion and frequency. Thermostatic control is turned on
M106 P1 S1 I0 F500 H-1 ; Set fan 1 value, PWM signal inversion and frequency. Thermostatic control is turned off
M106 P2 S1 I0 F500 H-1 ; Set fan 2 value, PWM signal inversion and frequency. Thermostatic control is turned off

; Custom settings are not configured

; Miscellaneous
T4 ; Select last tool

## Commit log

2017-12-29 Add files via upload
    Code for printing cylinder muscle
2019-06-02 add all files
    [dog_bones.g, dog_bones_muscle.g, polygon.g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]
2019-06-02 tidy up
    [dog_bones.g, dog_bones_muscle.g, polygon.g]
2019-06-03 add figures
    [config.g]
2019-06-03 add experiment data
    [Rheometer Data 35 A + B + Ethanol.xlsx, Rheometer Data 35 A + B + Thi_vex.xlsx, Rheometer Data 35 A + Ethanol.xlsx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]
2019-06-03 add model
    [30ml syringe holder_x4—v4.ipt, 3DPrinterBracket_Top_Long_1%2F8.ipt, 3DPrinterBracket_bottom_Long_1%2F8.ipt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]
2019-06-03 add data
    [Aslan_Test1.is_tcyclic_Results.csv, Aslan_Test1_a.is_tcyclic_Results.csv, Aslan_Test1_a_1.is_tcyclic_Results.csv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]
